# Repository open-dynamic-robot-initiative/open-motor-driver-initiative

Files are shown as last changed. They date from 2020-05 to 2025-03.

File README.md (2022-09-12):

# open-motor-driver-initiative
Open-source driver for brushless motors, following the open dynamic robot initiative 

This contains hardware and firmware for several open source motor control boards all based around TMS320F2838x MCU from Texas Instrument. The boards are designed to perform sensored FOC control of PMSM and BMDC motors.
The goal of this is to provide an alternative to close-sourced industrial grade motor controller that doesn't allow custom control design low, custom communication buses and sensor integration, as well as an alternative to open source low-cost projects that make many compromises and limit their performance.

This should only be replicated for specific needs, where bandwidth, power computation or sensor integration are needed. Often off-shelf solutions offer easier and lower cost solution. 

The TMS320F2838x offer a high number of peripheral dedicated to motor control as well as a fair bit of computational power with 3 CPUs and hardware accelerators. It also offers a range of high bandwidth communication buses such as SPI, FSI, EtherCAT, USART, CAN-FD, Ethernet, USB V2, etc. that allow to implement custom network ideal for centralised robotic applications. 

The main motivation for those boards is for them to be integrated into legged robotics to do academic research. 

All the content of this repository is under BSD-3 Licence.

## Several motor control boards
Several boards are developed around the same system architecture to accommodate different needs. (Number of axis, power ranges, from factor etc.)
See below an overview of the boards

[Todo put picture of all the boards, basic specs and link to the relevant folder]

### Texas Instrument development boards
This setup used TI dev board and was used for first development, It's not a very practical design
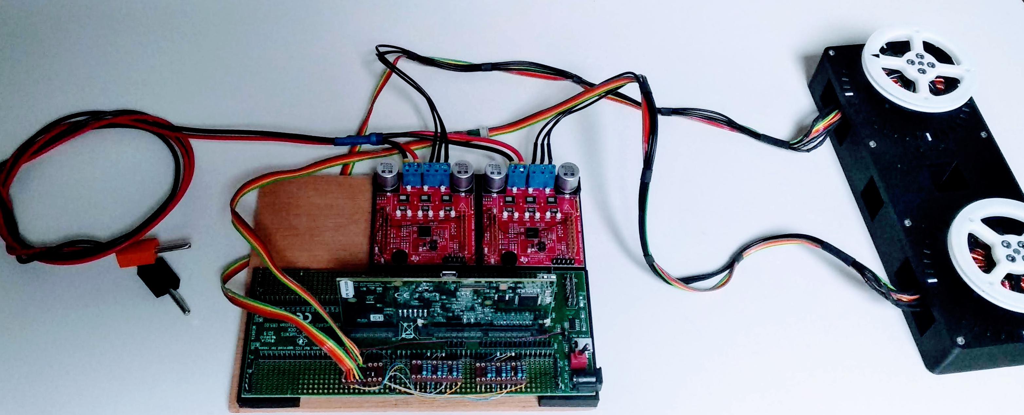
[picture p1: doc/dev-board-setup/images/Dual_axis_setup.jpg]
TI dev boars

### uOmodri (or udriverv3)
This board was design with to be backward compatible with the udriverv2 used in odri robots.
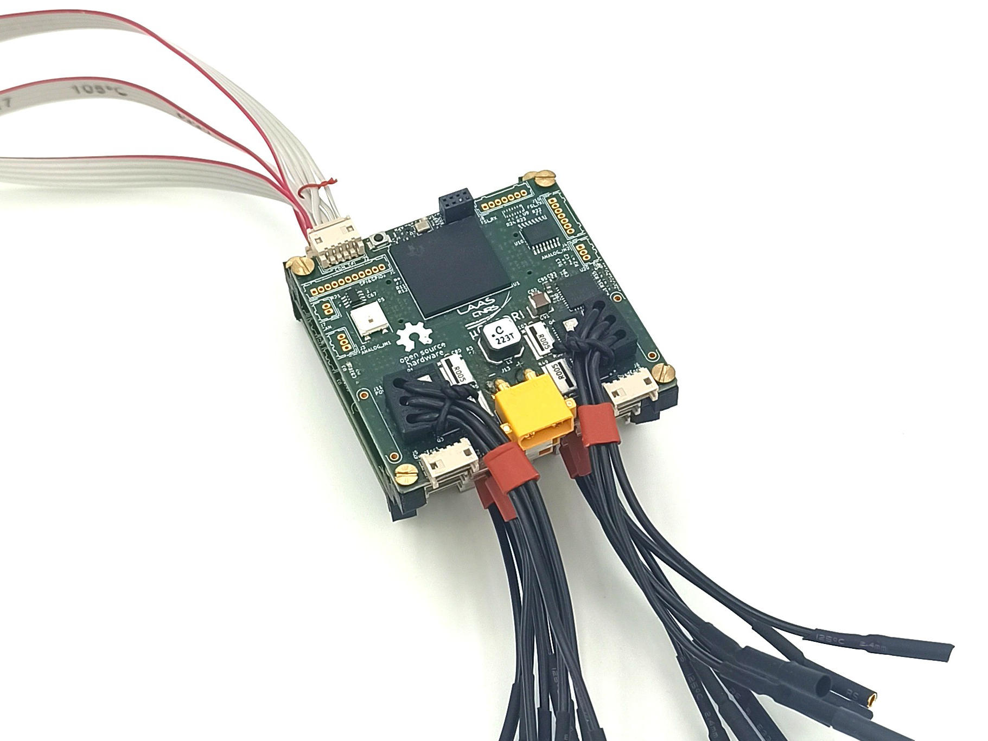
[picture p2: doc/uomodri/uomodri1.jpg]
uomodri

### uOmodri single axis
This board is a project not designed yet. It will be a single-axis version to be attached directly to motors from myactuator.com
### PAL Robotics MC21R01 
[to do]

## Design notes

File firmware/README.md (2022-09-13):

# Software for the Open Motor Driver Initiative project - uOmodri board

## Required installs
In order to use the UOMODRI projects, you must install [Code Composer Studio (CCS)](https://software-dl.ti.com/ccs/esd/documents/ccs_downloads.html) and [C2000Ware library](https://www.ti.com/tool/C2000WARE#downloads) from Texas Instruments. C2000Ware Motor Control SDK is not necessary anymore. 
The [installation](https://software-dl.ti.com/ccs/esd/documents/users_guide/index_installation.html) procedure is available on TI website.
For Linux users, don't forget to install USB drivers (everything is explained on Texas Instrument website).
When installing CCS, prefer a custom installation and check "C2000 real-time MCUs" installation.

## Repository description
This repository contains one project:
	**uOmodri_c28** : Main project. Implements current, speed and position control for PMSM along with a SPI communication for commands or debug. 
3 Files are mainly used for configuration:
- inc\uomodri_user_defines.h : Saves all the defines used in the project.
- inc\uomodri_hal_config_handlers.h : Structures necessaries during initialization phase.
- inc\uomodri_prj_config_handlers.h : Structures used in the running phase of the project.

## How to import these project
After cloning the repository, you can import the projects by doing Project > Import CCS project.
The last thing you must do before being able to compile the projects is to define the path to your C2000Ware library.
To do so, right click on the  project, and then Properties > Resource > Linked Resources.
Now modify the C2000WARE_ROOT path to match your own C2000Ware library folder path.
The folder should be named something like "C2000Ware_4_01_00_00" for the 4.01.00.00 version.
Verify that PARENT_LOC and WORKSPACE_LOC point on your own working workspace.

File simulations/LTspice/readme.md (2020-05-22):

LTspice XVII simulations.

To run the simulations you need to extract the files in the "Support Pack Rev 1.1.zip" and execute the files from inside the folder.

Support Pack Rev 1.1
Source: https://e2e.ti.com/support/archive/motor/m/spice/665327

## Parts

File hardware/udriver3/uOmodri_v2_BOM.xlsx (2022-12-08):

Reference | Value | Qty/PCB | Part No | Footprint | Mouser | DigiKey | Farnell | RS | STOCK
C4, C5, C6, C9, C10, C11, C30, C32, C33, C34, C35, C36, C43, C45, C46, C47, C48, C49 | 1.8nF | 18 | GRM033R71E182KA12D | Capacitor_SMD:C_0201_0603Metric | 81-GRM033R71E182KA2D | 490-GRM033R71E182KA12DTR-ND | 2999522 |  | 300
C29, C42 | 47nF | 2 | C1608X7S2A473K080AB | Capacitor_SMD:C_0603_1608Metric | 810-C1608X7S2A473K | 445-6032-1-ND | 2906791 |  | 100
C3, C7, C8, C12, C13, C14, C19, C20, C21, C22, C23, C26, C31, C39, C44, C50, C51, C52, C53, C54, C55, C69, C72, C73, C74, C75, C76, C77, C78, C79, C80, C81, C82, C83, C84, C85, C86, C87, C88, C89, C90, C91, C92, C93, C94, C99, C100, C101, C102, C103, C104 | 100nF | 51 | GRM033R61E104KE14J | Capacitor_SMD:C_0201_0603Metric | 81-GRM033R61E104KE4J | 490-14571-1-ND | 3790414 | 185-2066 | 1000
C58, C97 | 100nF | 2 | GRM188R72A104KA35D | Capacitor_SMD:C_0603_1608Metric | 81-GRM188R72A104KA35 | 490-3285-1-ND | 1828921 |  | 100+
C1, C2 | 220nF | 2 | GRM033R61C224KE14J | Capacitor_SMD:C_0201_0603Metric | 81-GRM033R61C224KE4J | 490-GRM033R61C224KE14JTR-ND | 3785715 |  | 100
C24, C27, C37, C40 | 1uF | 4 | C1005X5R1V105K050BE | Capacitor_SMD:C_0402_1005Metric | 810-C1005X5R1V105KE | 445-175218-1-ND | 3416060 |  | 150+
C28, C41, C61, C64, C67, C68, C71 | 1uF | 7 | GRM033C81A105ME05D | Capacitor_SMD:C_0201_0603Metric | 81-GRM033C81A105ME5D | 490-13219-1-ND | 3238032 |  | 250+
C25, C38 | 10uF | 2 | GRM188R61E106MA73D | Capacitor_SMD:C_0603_1608Metric | 81-GRM188R61E106MA3D | 490-7202-2-ND | 2695906 | 815-1377 | 100
C56, C57, C95, C96 | 10uF | 4 | C3225X7R1N106K250AC | Capacitor_SMD:C_1210_3225Metric | 810-C3225X7R1N106K25 | 445-C3225X7R1N106K250ACCT-ND | 3416259 |  | 100+
C60, C62, C63, C65, C66, C70 | 10uF | 6 | GRM155R60J106ME15D | Capacitor_SMD:C_0402_1005Metric | 81-GRM155R60J106ME5D | 490-13238-2-ND | 3582794 |  | 100
C15, C16, C17, C18 | 22uF | 4 | C5750X7S2A226M280KB | Capacitor_SMD:C_2220_5650Metric | 810-C5750X7S2A226280 | 445-C5750X7S2A226M280KBCT-ND | 3416277 |  | 60
C59, C98 | 22uF | 2 | GRM21BR61E226ME44L | Capacitor_SMD:C_0805_2012Metric | 81-GRM21BR61E226ME4L | 490-10749-2-ND | 1907510 | 247-8112 | 50
R31, R32, R39, R40, R41, R47 | 0.005 | 6 | FC4L32R005FER | udriver3:FC4L32 | 588-FC4L32R005FER | FC4L32R005FER-ND | 2420555 | 126-0360 | 100
R62, R64, R67, R68 | 10 | 4 | ERJ-1GNF10R0C | Resistor_SMD:R_0201_0603Metric | 667-ERJ-1GNF10R0C | P122669TR-ND | 2302282 | 179-7137 | 100
R18, R19, R20 | 100 | 3 | ERJ-1GNF1000C | Resistor_SMD:R_0201_0603Metric | 667-ERJ-1GNF1000C | P122654CT-ND | 2302309 | 179-7123 | 100+
R5, R6, R27, R30, R33, R34, R35, R42, R43, R44, R55, R56 | 120 | 12 | ERJ-1GNF1200C | Resistor_SMD:R_0201_0603Metric | 667-ERJ-1GNF1200C | P122692CT-ND | 2396857 |  | 200+
R58 | 909 | 1 | ERJ-1GNF9090C | Resistor_SMD:R_0201_0603Metric | 667-ERJ-1GNF9090C | P123194TR-ND | 3303125 |  | 100
R7, R8, R9, R10, R11, R12, R17, R37, R45 | 1k | 9 | ERJ-1GNF1001C | Resistor_SMD:R_0201_0603Metric | 667-ERJ-1GNF1001C | P122413CT-ND | 2302336 | 179-7127 | 200+
R50 | 2.49k | 1 | ERJ-1GNF2491C | Resistor_SMD:R_0201_0603Metric | 667-ERJ-1GNF2491C | P122865TR-ND | 3335222 |  | 100
R25 | 5.1k | 1 | ERJ-2RKF5101X | Resistor_SMD:R_0402_1005Metric | 667-ERJ-2RKF5101X | P5.10KLCT-ND | 2302709 | 732-5536 | 200+
R1, R2, R3, R4, R14, R15, R16, R21, R22, R23, R26, R28, R29, R36, R38, R46, R48, R57, R59, R60, R61, R65, R66 | 10k | 23 | ERJ-1GNF1002C | Resistor_SMD:R_0201_0603Metric | 667-ERJ-1GNF1002C | P122414CT-ND | 2302362 | 176-3597 | 400+
R52 | 22.1k | 1 | ERJ-1GNF2212C | Resistor_SMD:R_0201_0603Metric | 667-ERJ-1GNF2212C | P122837CT-ND | 3335196 |  | 100+
R13, R49, R51, R53, R54 | 100k | 5 | ERJ-1GNF1003C | Resistor_SMD:R_0201_0603Metric | 667-ERJ-1GNF1003C | P122655CT-ND | 2302389 | 179-7130 | 200+
R24 | 100k | 1 | ERJ-2RKF1003X | Resistor_SMD:R_0402_1005Metric | 667-ERJ-2RKF1003X | P100KLCT-ND | 2302839 | 732-5255 | 200+
FB1, FB2, FB3 | 220R@100MHz | 3 | BLM18SG221TN1D | Inductor_SMD:L_0603_1608Metric | 81-BLM18SG221TN1D | 490-5225-1-ND | 1515753 | 792-6271 | 100
U1, U2, U3, U19 | 74LVC2G17 | 4 | 74LVC2G17GM,115 | udriver3:SOT886_USON_6_1.45x1.0mm_P0.5mm | 771-LVC2G17GM115 | 1727-7017-2-ND |  |  | 50
J8, J9 | ADM6_ADF6 | 2 | ADF6-10-03.5-L-4-2-A | udriver3:ADF6-10-XX.X-XXX-4-X-A-XR | 200-ADF6-10-3.5-L42A | 612-ADF6-10-03.5-L-4-2-A-TR-ND | 3462763 | 202-7885
SW1 | B3U-3100P-B | 1 | B3U-1000P-B | Button_Switch_SMD:SW_SPST_B3U-1000P-B | 653-B3U-1000P-B | SW1143TR-ND | 1333654 |  | 50
D2 | BAT54L | 1 | BAT54L,315 | Diode_SMD:D_0402_1005Metric | 771-BAT54L-T/R | 2156-BAT54L,315-954-ND | 2438976 |  | 25
U16 | BMI088 | 1 | BMI088 | udriver3:Bosch_LGA-16_4.5x3.0mm_P0.5mm | 262-BMI088 | 828-1082-2-ND |  |  | 5+10
J6 | Conn_01x02 | 1 |  | udriver3:AMASS_XT30PW-M_1x02_P2.50mm_Horizontal
J13 | conn_01x02_MountingPins | 1 | DF13-2P-1.25H(76) | udriver3:Hirose_DF13_02P-1.25H_1x02_P1.25mm_Right_angle | 798-DF13-2P-1.25H76 | H126390-ND |  | 188-5752 | 30
J10, J11 | Conn_01x03 | 2 |  | udriver3:AMASS_MR30PW-FB_1x03_P3.50mm_Horizontal
J1 | conn_01x04_MountingPins | 1 | DF13-4P-1.25H(76) | udriver3:Hirose_DF13_04P-1.25H_1x05_P1.25mm_Right_angle | 798-DF13-4P-1.25H76 | H126400-ND | 2916344 | 188-6267 | 30
J2, J3, J14 | conn_01x05_MountingPins | 3 | DF13-5P-1.25H(76) | udriver3:Hirose_DF13_05P-1.25H_1x05_P1.25mm_Right_angle | 798-DF13-5P-1.25H76 | H126405-ND | 3019728 | 188-6306 | 100
J4, J5 | conn_01x08_MountingPins | 2 | 5034800800 | udriver3:Molex_FBH1_1x08-2MP_P0.50mm_Horizontal | 538-503480-0800 | WM1388TR-ND | 2396218 | 896-7614 | 50
J12 | Conn_01x10 | 1 | DF13-10P-1.25DSA | udriver3:Hirose_DF13-10P-1.25DSA_1x10_P1.25mm_Vertical | 798-DF13-10P-1.25DSA | H2198-ND |  | 188-6354 | 11+10
J7 | Conn_02x04_Odd_Even | 1 | 20021311-00008T4LF | udriver3:PinSocket_2x04_P1.27mm_Vertical | 649-221311-00008T4LF | 609-3753-ND | 2892503 |  | 40
Q2, Q3, Q4, Q5, Q6, Q7 | CSD88599Q5DC | 6 | CSD88599Q5DC | udriver3:VSON_CLIP_22 | 595-CSD88599Q5DC | 296-48289-1-ND | 2766880 |  | 130 + 50 (CSD88584)
U9, U10 | DRV8353S | 2 | DRV8353SRTAT | Package_DFN_QFN:QFN-40-1EP_6x6mm_P0.5mm_EP4.6x4.6mm_ThermalVias | 595-DRV8353SRTAT | 296-DRV8353SRTATCT-ND |  |  | 11+50(SMRTAT)
U4 | DSLVDS1047 | 1 | DSLVDS1047PWR | Package_SO:TSSOP-16_4.4x5mm_P0.65mm | 595-DSLVDS1047PWR | 296-50740-1-ND |  |  | 50
U5 | DSLVDS1048 | 1 | DSLVDS1048PWR | Package_SO:TSSOP-16_4.4x5mm_P0.65mm | 595-DSLVDS1048PWR | 296-51106-1-ND |  |  | 35
X1 | ECS-TXO-2016 | 1 | ECS-TXO-2016-33-250-TR | udriver3:TCXO_SMD_Ecs_TXO-2016-4Pin_2.0x1.6mm | 520-TXO-2016-33-250T | XC3163TR-ND | 4059413 |  | 50
D11, D12 | ESD321 | 2 | ESD321DPYR | Diode_SMD:D_0402_1005Metric | 595-ESD321DPYR | 296-51108-1-ND |  |  | 100+
D6 | LED GREEN | 1 | HSMG-C280 | LED_SMD:LED_0402_1005Metric | 630-HSMG-C280 | 516-3066-1-ND | 2494322 | 867-6560 | 200
D9, D10 | LED RED | 2 | HSMC-C280 | LED_SMD:LED_0402_1005Metric | 630-HSMC-C280 | 516-3060-1-ND | 2494321 |  | 100
U14 | LT6654AIS6-3 | 1 | LT6654AIS6-3#TRMPBF | Package_TO_SOT_SMD:TSOT-23-6 | 584-6654AIS63TRMPBF | LT6654AIS6-3#TRMPBFCT-ND | 2761957 |  | 35
U12, U13 | MPM3804GG | 2 | MPM3804GG | udriver3:QFN-10_2x2mm_P0.5mm | 946-MPM3804GG-Z | 1589-1982-1-ND | 3358188 |  | 100
Q1 | NX7002BKM | 1 | NX7002BKMYL | Package_DFN_QFN:Diodes_DFN1006-3 | 771-NX7002BKMYL | 1727-2232-1-ND | 2498574 |  | 50
U17 | TCAN330G | 1 | TCAN330GDCNR | Package_TO_SOT_SMD:TSOT-23-8 | 595-TCAN330GDCNR | 296-TCAN330GDCNRTR-ND | 3009407 |  | 50
U18 | THVD24x0 | 1 | THVD2450DRBR | udriver3:VSON-8-1EP_3.0x3.0mm_P0.65mm_EP1.65x2.4mm | 595-THVD2450DRBR | 296-THVD2450DRBRTR-ND |  |  | 50
U6 | TMS320F28388D | 1 | F28388DZWTS | udriver3:NFBGA_337 | 595-F28388DZWTS | 296-F28388DZWTS-ND |  |  | 20 + 18(F28386)
D5, D7, D8 | TPD1E04U04 | 3 | TPD1E04U04DPLT | Diode_SMD:D_0402_1005Metric | 595-TPD1E04U04DPLT | 296-47862-1-ND |  |  | 50
D1, D3 | TPD6E05U06 | 2 | TPD6E05U06RVZR | udriver3:USON_14 | 595-TPD6E05U06RVZR | 296-39349-1-ND |  |  | 200
U8 | TPS3703-1.2 | 1 | TPS3703A7120DSERQ1 | Package_SON:WSON-6_1.5x1.5mm_P0.5mm | 595-S3703A7120DSERQ1 | 296-TPS3703A7120DSERQ1CT-ND |  |  | 50
U7 | TPS3703-3.3 | 1 | TPS3703A7330DSERQ1 | Package_SON:WSON-6_1.5x1.5mm_P0.5mm | 595-S3703A7330DSERQ1 | 296-TPS3703A7330DSERQ1CT-ND |  |  | 50
U15 | TPSM560R6H | 1 | TPSM560R6HRDAR | udriver3:B3QFN_15 | 595-TPSM560R6HRDAR | 296-TPSM560R6HRDARTR-ND |  |  | 50
U11 | TPSM5601R5 | 1 | TPSM5601R5RDAR | udriver3:B3QFN_15 | 595-TPSM5601R5SRDAR | 296-TPSM5601R5RDARTR-ND |  |  | 50
J15 | USB_B_Micro | 1 | 473460001 | udriver3:USB_Micro-B_Molex_47346-0001 | 538-47346-0001 | WM17141CT-ND | 1568026 | 702-5475 | 30
D4 | WS2812B | 1 | WS2812B 5050 | LED_SMD:LED_WS2812B_PLCC4_5.0x5.0mm_P3.2mm | 474-COM-16346 | 1568-COM-16347CT-ND |  |  | 50

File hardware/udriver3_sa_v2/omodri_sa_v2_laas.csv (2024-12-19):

Id | Designator | Footprint | Quantity | Designation | Supplier and ref
1 | C51,C45 | C_0402_1005Metric | 2 | 1u
2 | C50,C48,C66,C63,C65,C70,C102,C101,C62,C64,C2,C61,C67,C27,C6,C5,C9,C4,C25,C29,C28,C69,C21,C31,C30,C68,C22,C19,C20,C24,C23,C26,C13,C16,C38,C7,C14,C42,C87,C18,C3,C37,C41,C8,C15,C17 | C_0201_0603Metric | 46 | 100n
3 | C76,C71,C75,C74,C72,C73 | C_1206_3216Metric | 6 | 4.7u
4 | C53 | C_0603_1608Metric | 1 | 47n
5 | C52,C100,C10,C11,C32,C34,C33,C43,C35,C39 | C_0201_0603Metric | 10 | 1u
6 | C55,C47,C104,C97,C60,C58,C57,C59 | C_0201_0603Metric | 8 | 1.8n
7 | FB3,FB1,FB2 | R_0603_1608Metric | 3 | 220
8 | R1,R52,R30,R54,R8,R9,R10,R25,R35,R33,R34,R32,R11,R29,R12,R36,R26,R31,R6 | R_0201_0603Metric | 19 | 10k
9 | U13,U14 | QFN-10_2x2mm_P0.5mm | 2 | MPM3804GG-Z
10 | R27,R16,R19 | FC4L32 | 3 | 0.005
11 | U5 | UQFN-10_1.5x2mm_P0.5mm | 1 | TS3USB221E
12 | Q1,Q2,Q3 | VSON_CLIP_22 | 3 | CSD88599Q5DC
13 | R43,R44,R49,R46,R48,R40,R41 | R_0201_0603Metric | 7 | 100k
14 | R15,R18,R21 | R_0805_2012Metric | 3 | 4.7
15 | R50 | R_0201_0603Metric | 1 | 6.84k
16 | U7 | Bosch_LGA-16_4.5x3.0mm_P0.5mm | 1 | BMI088
17 | R37,R51,R24,R13,R14,R23,R22,R4 | R_0201_0603Metric | 8 | 120
18 | R53 | R_0201_0603Metric | 1 | 6.22k
19 | U4 | SOT-23-8 | 1 | TCAN3414
20 | R45 | R_0201_0603Metric | 1 | 13.7k
21 | Q4 | Diodes_DFN1006-3 | 1 | NX7002BKM
22 | C49,C91,C90,C92,C89 | C_0603_1608Metric | 5 | 10u
23 | D6 | LED_0402_1005Metric | 1 | LED GREEN
24 | U12 | uSIP_11 | 1 | TPSM8290x
25 | J3 | SAMTEC_CLP-104-02-L-D-BE | 1 | SAMTEC_CLP_02x04_SMD
26 | R2,R3,R5,R7 | R_0201_0603Metric | 4 | 10
27 | X1 | TCXO_SMD_Ecs_TXO-2016-4Pin_2.0x1.6mm | 1 | ECS-TXO-2016
28 | C93,C99,C96,C94,C44,C98,C95,C40,C36,C12 | C_0402_1005Metric | 10 | 10u
29 | U1 | NFBGA_337 | 1 | TMS320F28388D
30 | U15 | TSOT-23-6 | 1 | LT6654AIS6-3
31 | D5,D4 | NeoPixel_SK6805_1.5x1.5mm | 2 | NeoPixel_1515
32 | D2,D7,D1 | D_0201_0603Metric | 3 | TPD1E04U04
33 | U2 | QFN-40-1EP_6x6mm_P0.5mm_EP4.6x4.6mm | 1 | DRV8353S
34 | C88 | C_0603_1608Metric | 1 | 100n
35 | SW1 | SW_SPST_B3U-1000P-B | 1 | B3U-1000P-B
36 | R47 | R_0201_0603Metric | 1 | 22.1k
37 | TP1 | TestPoint_Keystone_5015_Micro-Minature | 1 | GND
38 | U16 | SOT-353_SC-70-5 | 1 | OPA333xxDCK
39 | C103,C1 | C_0201_0603Metric | 2 | 220n
40 | C82,C83,C77,C86,C84,C85,C81,C79,C80,C78 | C_1210_3225Metric | 10 | 10u
41 | C54,C46,C56 | C_0402_1005Metric | 3 | 4.7n
42 | R20,R28,R17 | R_0805_2012Metric | 3 | 2.2
43 | R38 | R_0402_1005Metric | 1 | 100k
44 | U8 | SOT886_USON_6_1.45x1.0mm_P0.5mm | 1 | 74LVC1G17
45 | R42 | R_0201_0603Metric | 1 | 9.09k
46 | R39 | R_0402_1005Metric | 1 | 5.1k
47 | U9 | WSON-6_1.5x1.5mm_P0.5mm | 1 | TPS3703-3.3
48 | U10 | WSON-6_1.5x1.5mm_P0.5mm | 1 | TPS3703-1.2
49 | J2 | Molex_FBH1_FFC_FPC_503480-2000_1x20-2MP_P0.50mm_Horizontal | 1 | conn_01x20_MountingPins
50 | D3 | TI_X2SON-3_1.3x0.6mm_P1.0mm | 1 | ESD122
51 | U6 | VSON-8-1EP_3.0x3.0mm_P0.65mm_EP1.65x2.4mm | 1 | THVD2450
52 | U11 | B3QFN_15 | 1 | TPSM560R6H
53 | U3 | TSSOP-14_4.4x5mm_P0.65mm | 1 | AS5047U

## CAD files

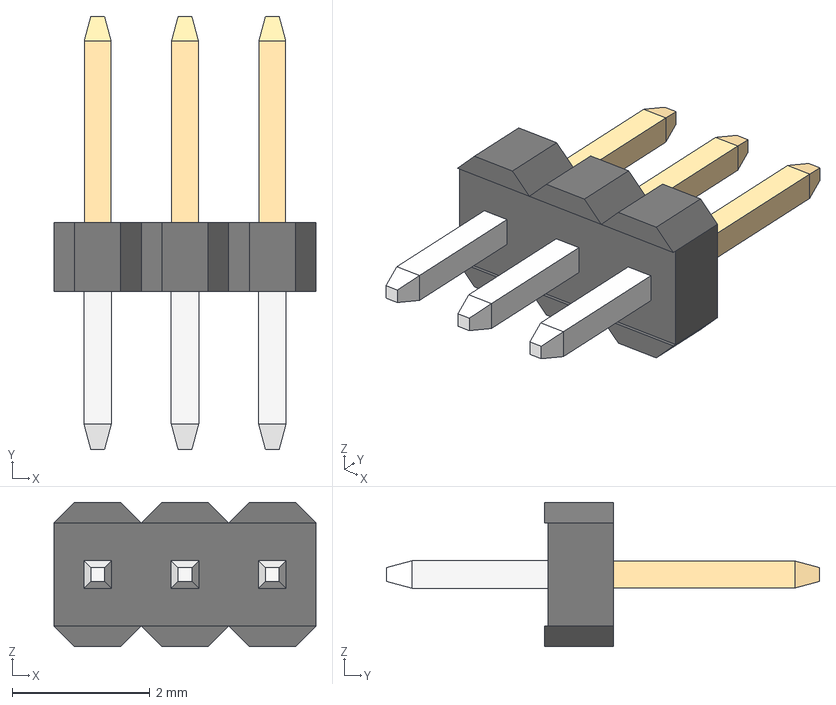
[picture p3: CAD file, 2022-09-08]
hardware/EcatExBrd/3D/Harwin_3P_m50-3530342_asm.stp
3.81 x 6.30 x 2.10 mm
M50-35303_MOULD
M50-353_CONTACT x 3

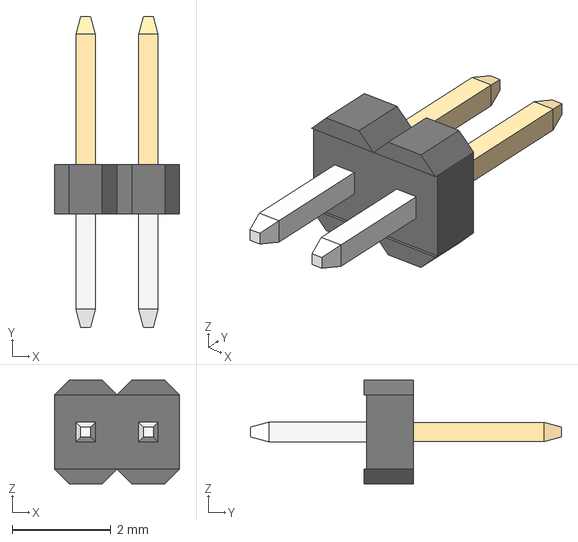
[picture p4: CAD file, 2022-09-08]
hardware/EcatExBrd/3D/Harwin_2P_m50-3530242_asm.stp
2.54 x 6.30 x 2.10 mm
M50-35302_MOULD
M50-353_CONTACT x 2

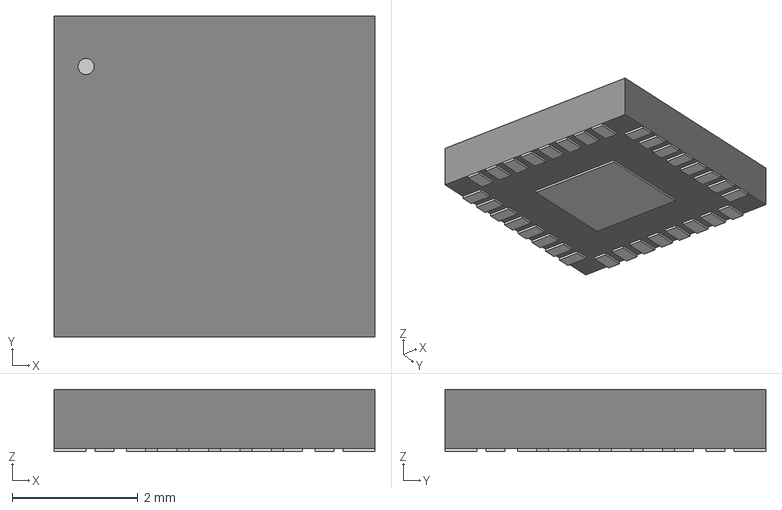
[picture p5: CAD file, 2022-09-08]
hardware/EcatExBrd/3D/QFN_ERHBR_TEX-L.step
5.11 x 5.11 x 0.993 mm

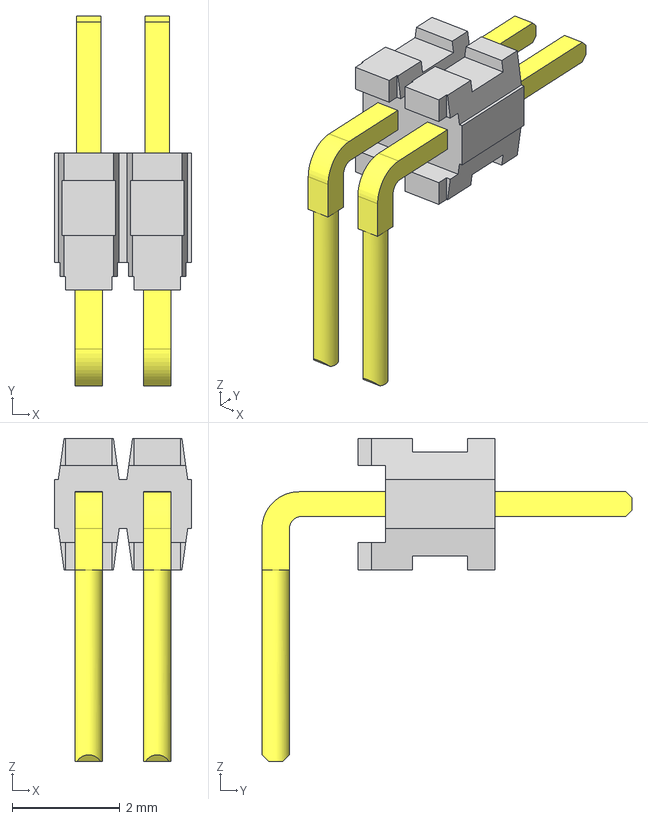
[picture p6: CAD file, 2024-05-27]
hardware/udriver3/3D/SAMTEC_TMS-102-02-G-S-RA.stp
2.54 x 6.86 x 5.99 mm
TMS-102-S_header
T-1M6-02-02-S-RA

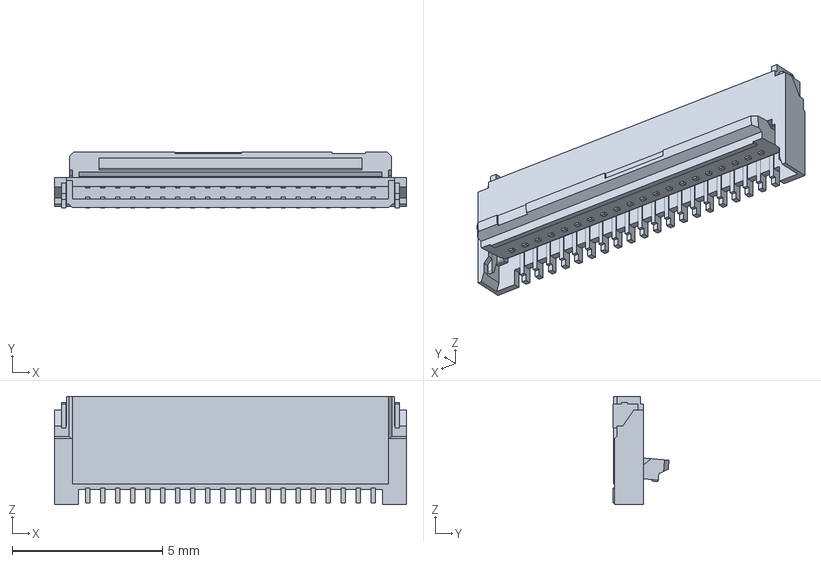
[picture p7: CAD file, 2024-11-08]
hardware/udriver3_sa_v2/3D/MOLEX_5034802000.stp
11.7 x 1.87 x 3.60 mm

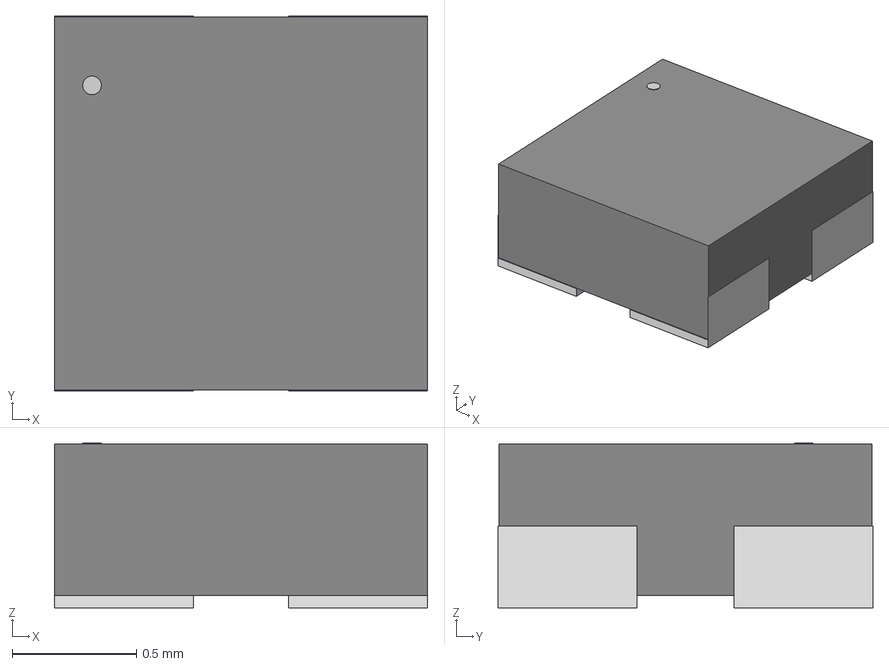
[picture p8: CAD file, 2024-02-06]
hardware/udriver3/3D/NeoPixel_1515_SK6805.step
1.50 x 1.51 x 0.663 mm

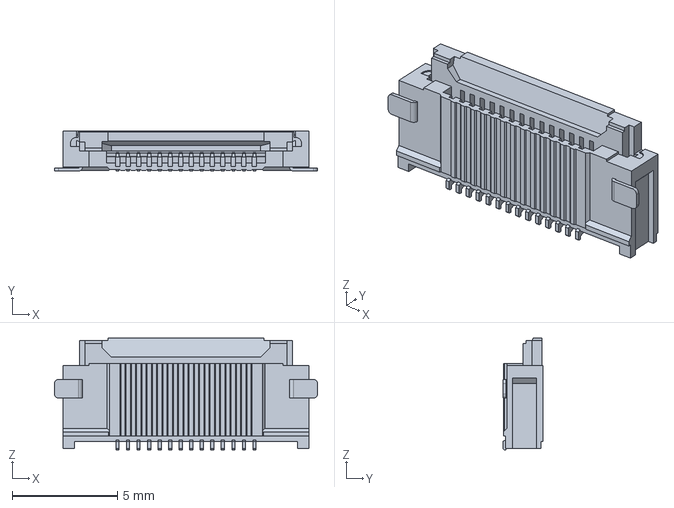
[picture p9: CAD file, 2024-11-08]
hardware/udriver3_sa_v2/3D/MOLEX_5051101497.stp
12.5 x 1.90 x 5.30 mm

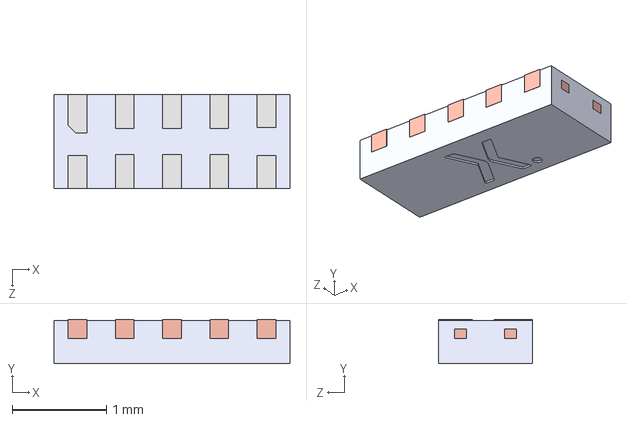
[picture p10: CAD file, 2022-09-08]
hardware/EcatExBrd/3D/Nexperia_IP4283CZ10_DFN2510A-10_SOT1176.step
2.50 x 0.47 x 1.00 mm
SOT1176 LF
SOT1176 Mold body

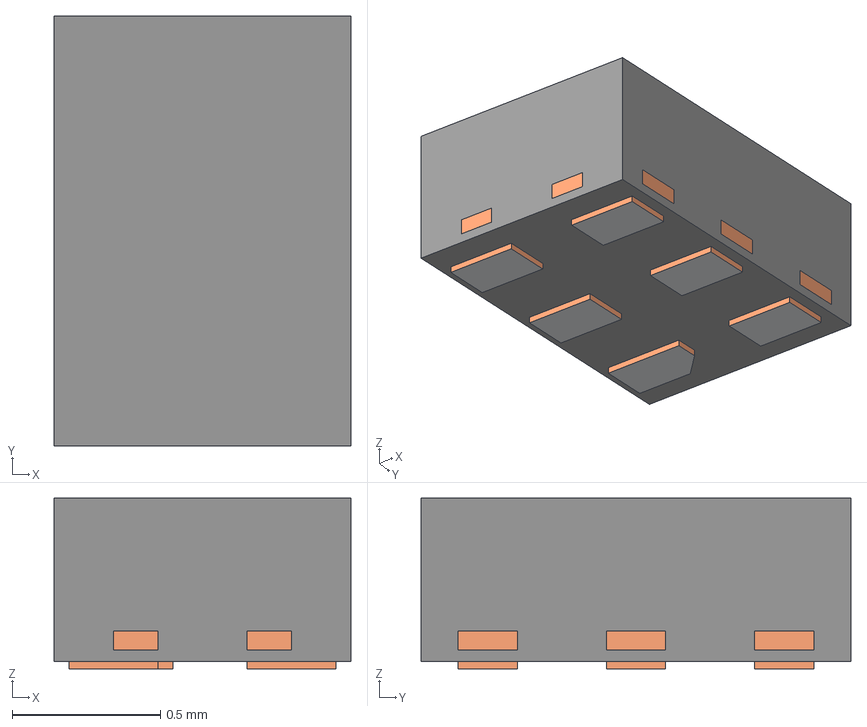
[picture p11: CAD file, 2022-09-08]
hardware/udriver3/3D/DRY0006A.stp
1.00 x 1.45 x 0.575 mm
BODY-SON
FRAME-DRY0006A
PIN1-ID

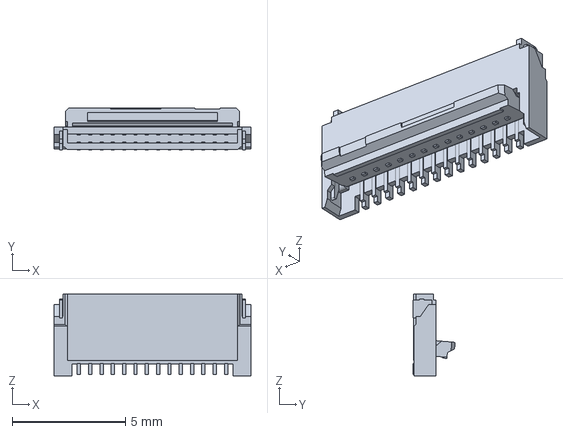
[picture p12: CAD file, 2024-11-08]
hardware/udriver3_sa_v2/3D/MOLEX_5034801400.stp
8.70 x 1.87 x 3.60 mm

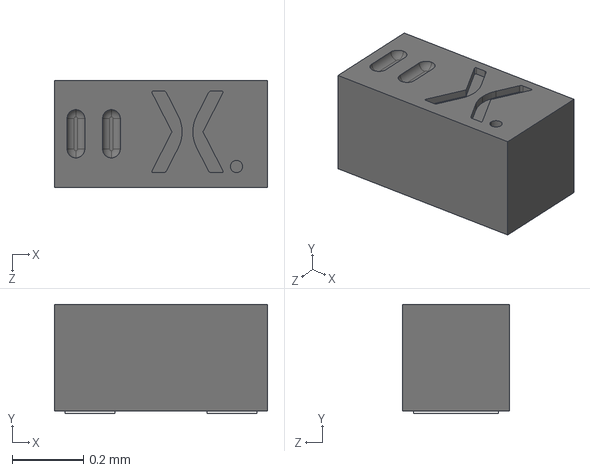
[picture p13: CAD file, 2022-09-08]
hardware/EcatExBrd/3D/Nexperia_PESD6V5C1USF_DSN0603-2_SOD962.step
0.6 x 0.308 x 0.3 mm

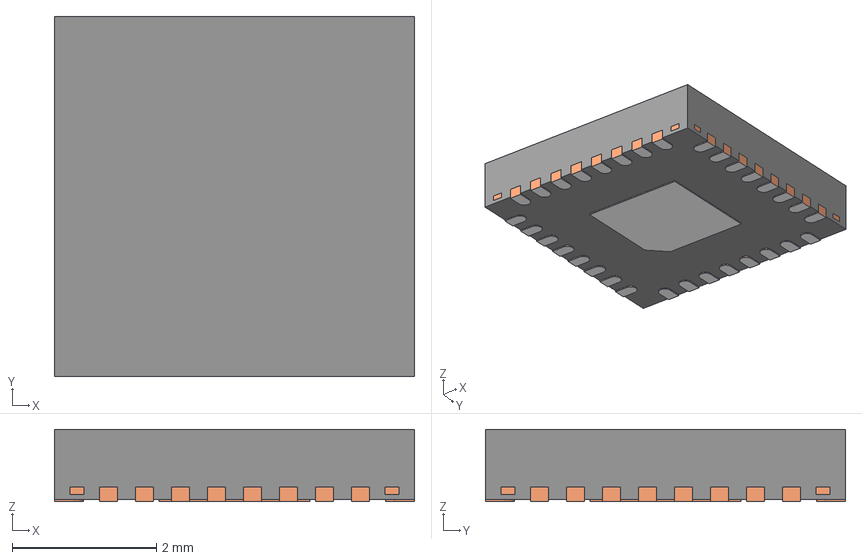
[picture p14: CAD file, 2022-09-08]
hardware/EcatExBrd/3D/RHB0032M.stp
5.00 x 5.00 x 1.00 mm
BODY-QFN
FRAME-RHB0032M
PIN1-ID

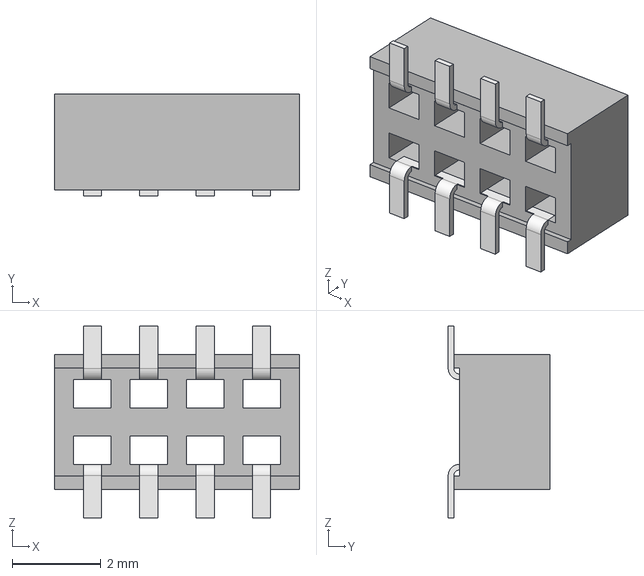
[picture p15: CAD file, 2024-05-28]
hardware/udriver3_sa_v2/3D/SAMTEC_CLP-104-02-L-D-BE.stp
5.51 x 2.29 x 4.32 mm
CLP-104-2-L-D-BE_terminal
C-106-22-1-L-04-BE_Pin x 2

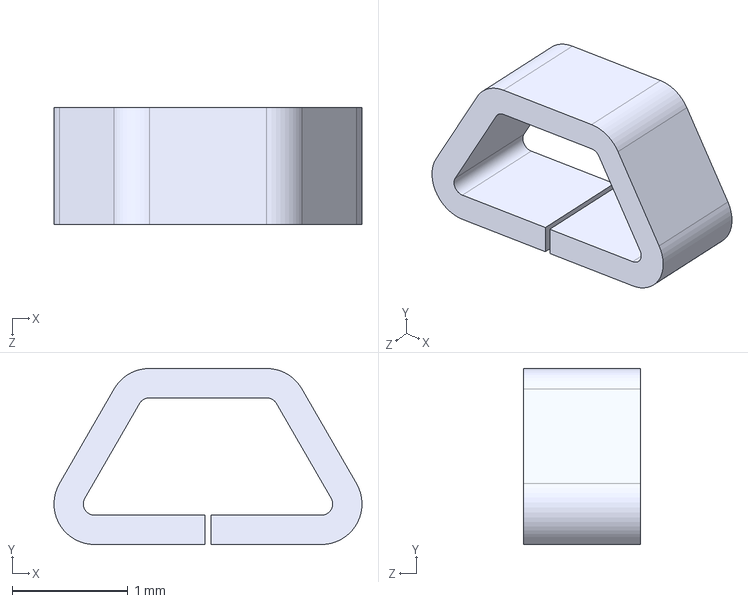
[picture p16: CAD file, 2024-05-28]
hardware/udriver3_sa_v2/3D/KEYSTONE_5015.step
2.67 x 1.52 x 1.02 mm

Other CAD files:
hardware/udriver3_sa_v2/3D/MOLEX_5051101492.stp
hardware/EcatExBrd/3D/QFN_ERHBR_TEX.step
hardware/EcatExBrd/3D/ADM6-10-01.5-L-4-2-A-TR.stp
hardware/udriver3_sa_v2/3D/KEYSTONE_5019.step
hardware/EcatExBrd/3D/DF13-6P-1.25DSA.stp
hardware/EcatExBrd/3D/DF13-8P-1.25DSA.stp
hardware/EcatExBrd/3D/MagJack_RJ45_Molex_480749101.stp
hardware/EcatExBrd/3D/Maxim_max147xx_TDFN8_1EP.step
hardware/EcatExBrd/3D/Maxim_max3107_TQFN24.step
hardware/EcatExBrd/3D/QFN_ERHBR_TEX-M.step
hardware/udriver3_sa_v2/3D/AMASS_MR30PB-FB.step
hardware/udriver3_sa_v2/3D/AMASS_MR30PW-FB.STEP
hardware/udriver3_sa_v2/3D/AMASS_MR30PW-M.STEP
hardware/udriver3_sa_v2/3D/AMASS_XT30PW-M.STEP
hardware/udriver3_sa_v2/3D/AMPHENOL_10165448-00008.stp
hardware/udriver3_sa_v2/3D/ASTX-H12.STEP
hardware/udriver3_sa_v2/3D/BOSCH_BMI088.STEP
hardware/udriver3_sa_v2/3D/C5750X7S2A226M280KB.STEP
hardware/udriver3_sa_v2/3D/Coilcraft-LPS6235.STEP
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

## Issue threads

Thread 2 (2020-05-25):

Labeling error in OMODRI_EtherCAT_x

Jmanhes, 2020-05-25:
In OMODRI_EtherCAT_0 & OMODRI_EtherCAT_1 there is twice the same label : Led0/Strap2.
Must be rename.

Jmanhes, 2020-05-25:
In OMODRI_Support, R193/R194 are connected to U23.
According to CDCLVC1104 datasheet [https://www.ti.com/lit/ds/symlink/cdclvc1104.pdf?ts=1590417975450](url), page 10/32, Table 1 : output logic table.
If 1G=L =>Yn=L whatever CLKin
if 1G=H => Yn=CLKin
So R194/R193 can be removed and pin can by tied to VDD_3V3

Jmanhes, 2020-06-22:
Correction done.

Closed 2020-06-22.

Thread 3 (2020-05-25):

Extra resistors can be removed in OMODRI_Support

Jmanhes, 2020-05-25:
In OMODRI_Support, R193/R194 are connected to U23.
According to CDCLVC1104 datasheet https://www.ti.com/lit/ds/symlink/cdclvc1104.pdf?ts=1590417975450, page 10/32, Table 1 : output logic table.
If 1G=L =>Yn=L whatever CLKin
if 1G=H => Yn=CLKin
So R194/R193 can be removed and pin can by tied to VDD_3V3

nswdc, 2020-07-06:
Closed by comit ba2ab1a811792042321e827a74f1fd63dcaec834

Closed 2020-07-06.

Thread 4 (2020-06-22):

Pin changes

otrebla333, 2020-06-22:
Review pin affectation list to make space for using all available SPI pins and for easing the routing of the EtherCAT lines. Affected pins are:
-Quadrature encoder 2 (move to other space)
- DRV1: nFault
- DRV2: Enable, CS, nFault

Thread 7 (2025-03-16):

Is posible control motor by step/dir??

artayasa, 2025-03-16:
Hi mate
Is posible to control the motor by step/dir?? I want to coustem the power bridge to handle 110v-220v i wamt run pmsm motor by step/dir mate, with abz encoder 20bit or 2000ppr.

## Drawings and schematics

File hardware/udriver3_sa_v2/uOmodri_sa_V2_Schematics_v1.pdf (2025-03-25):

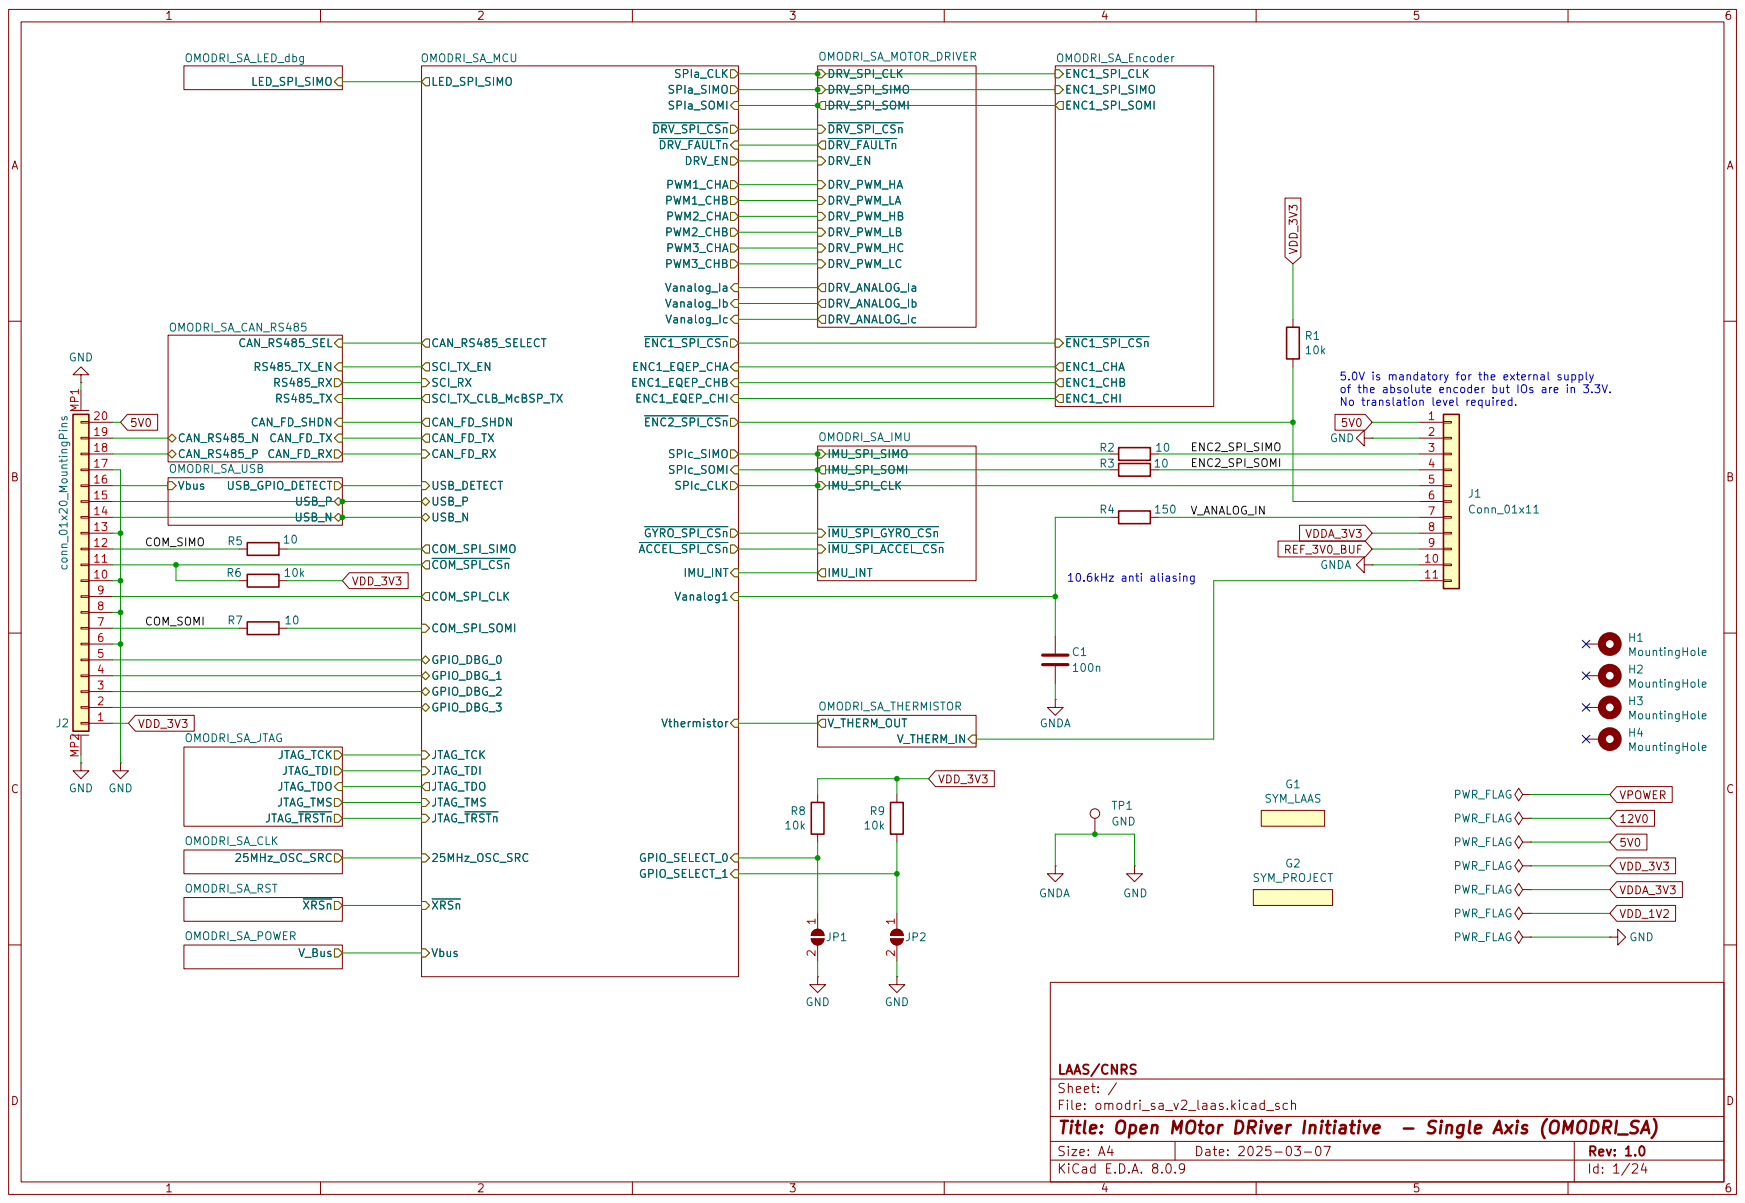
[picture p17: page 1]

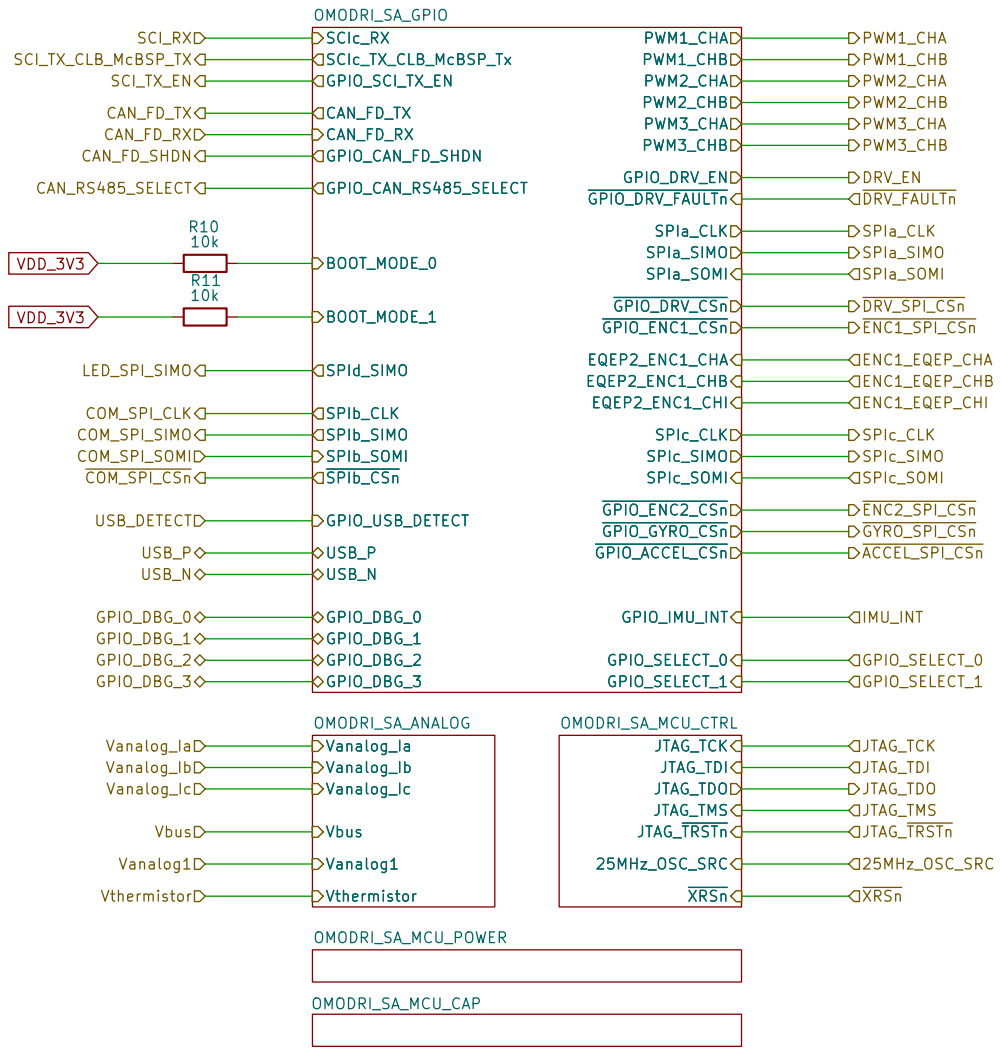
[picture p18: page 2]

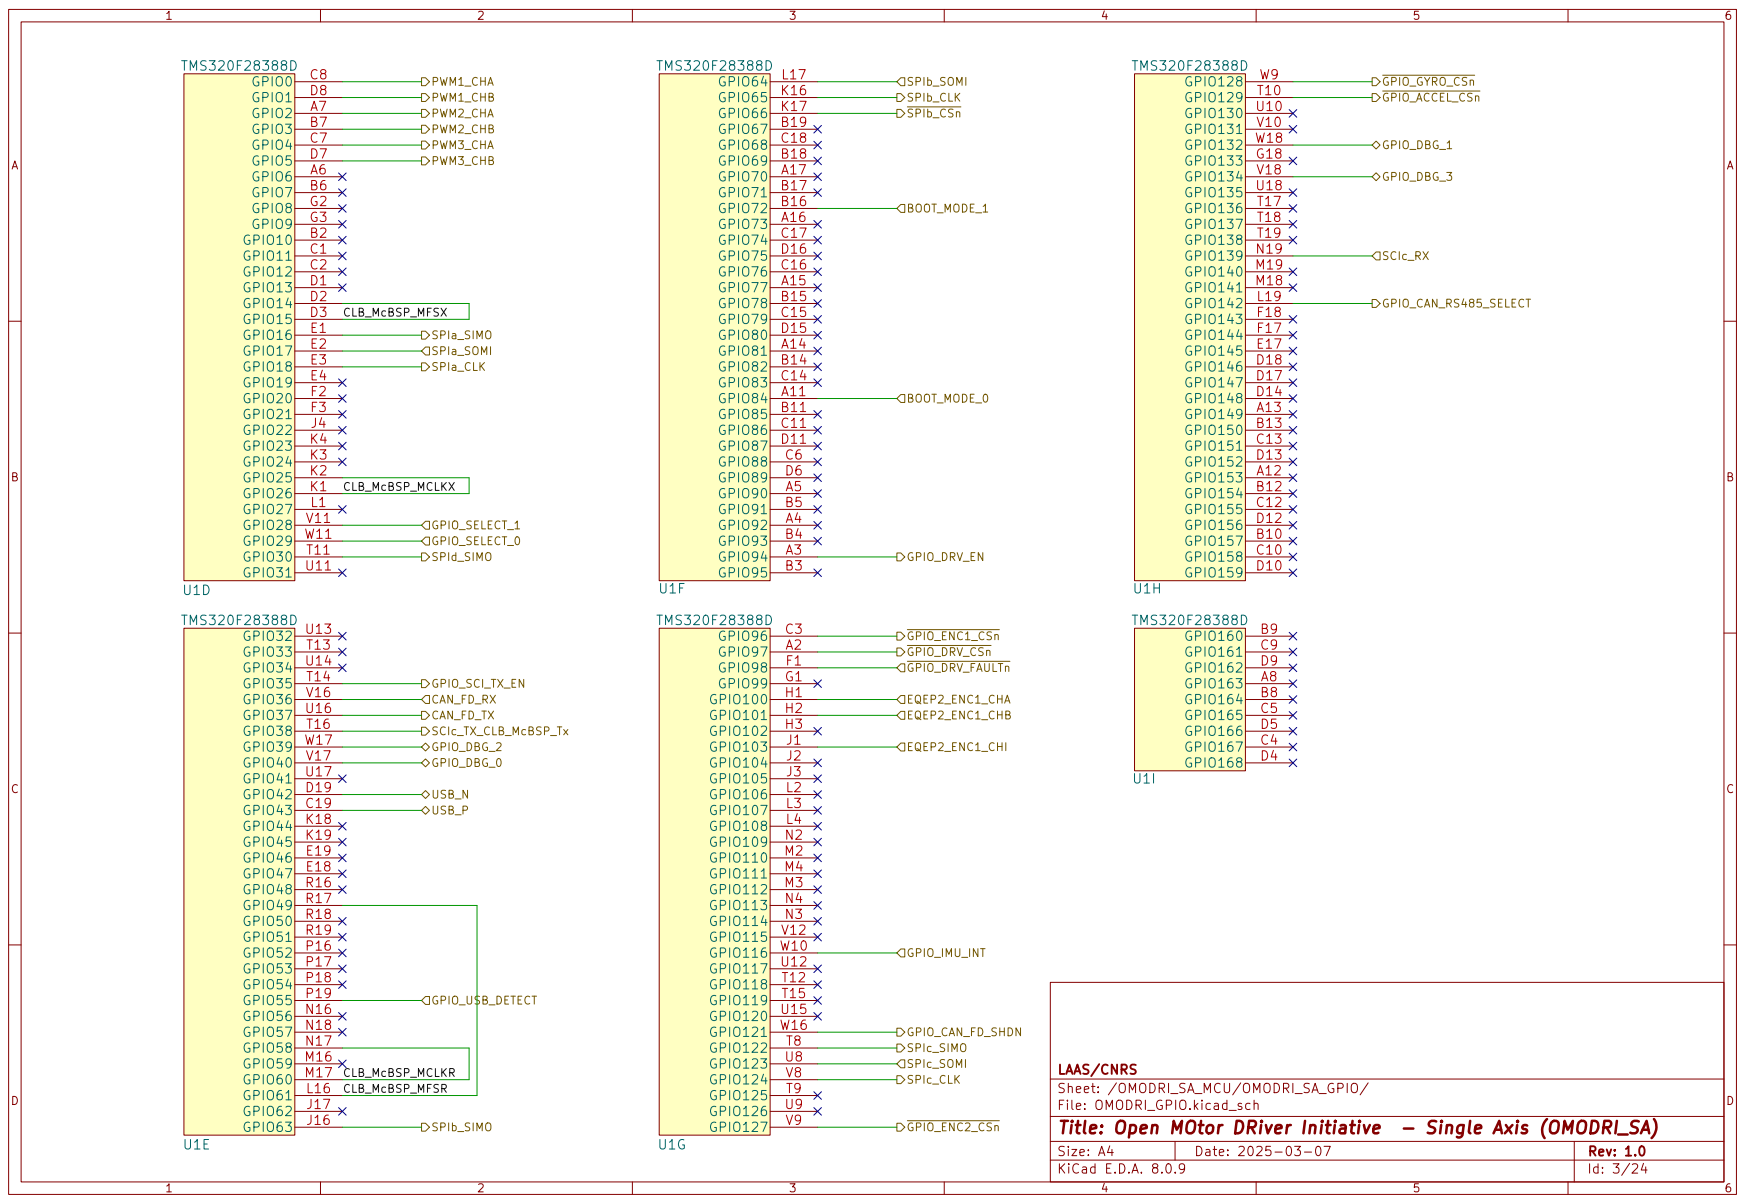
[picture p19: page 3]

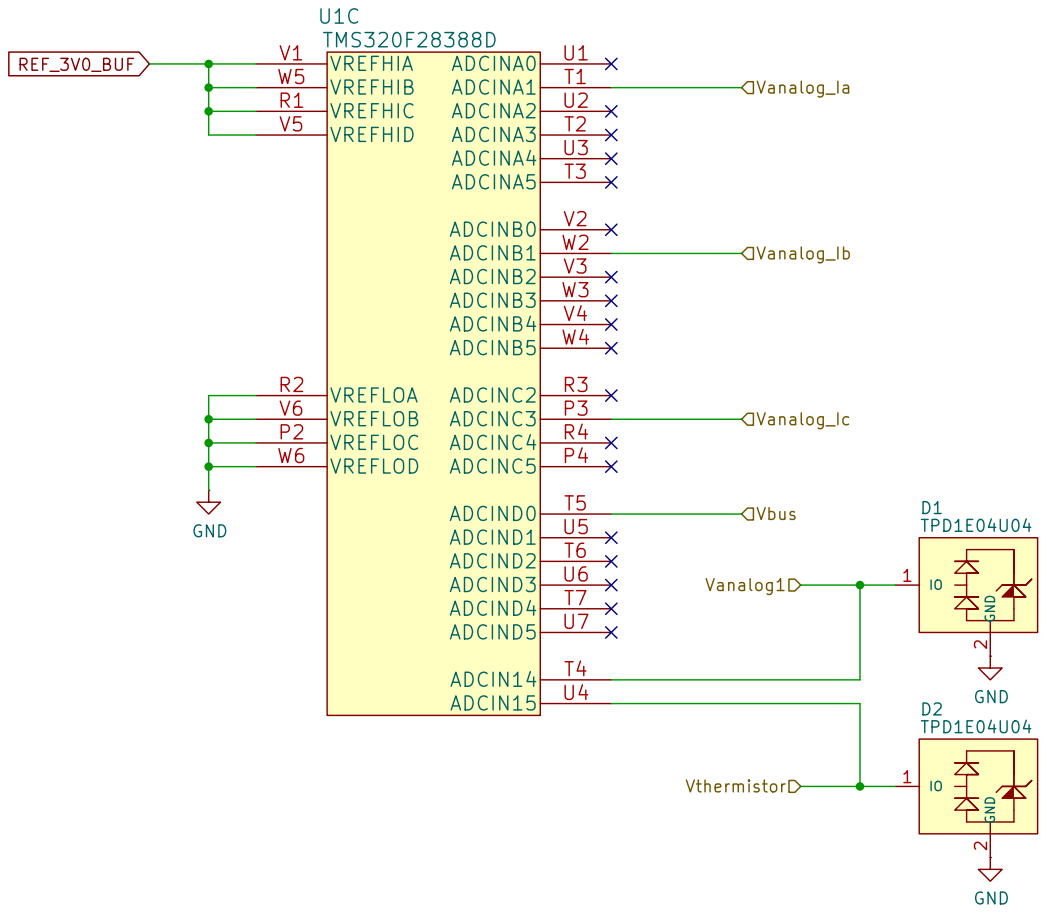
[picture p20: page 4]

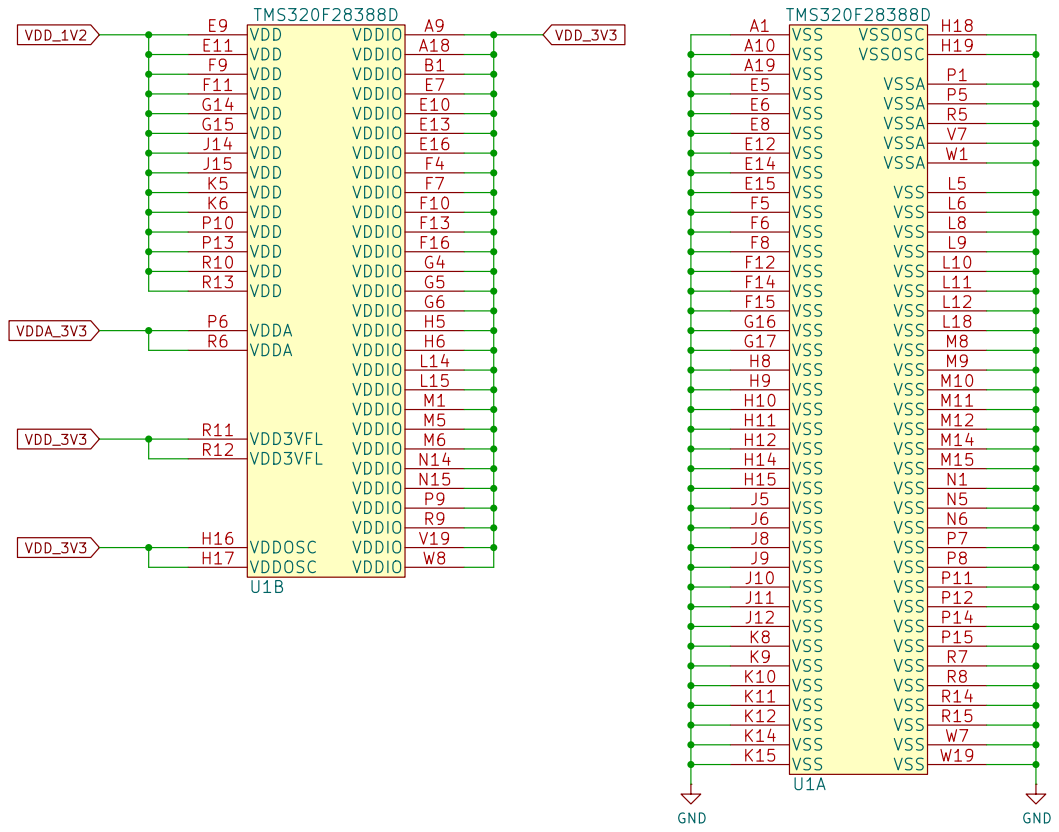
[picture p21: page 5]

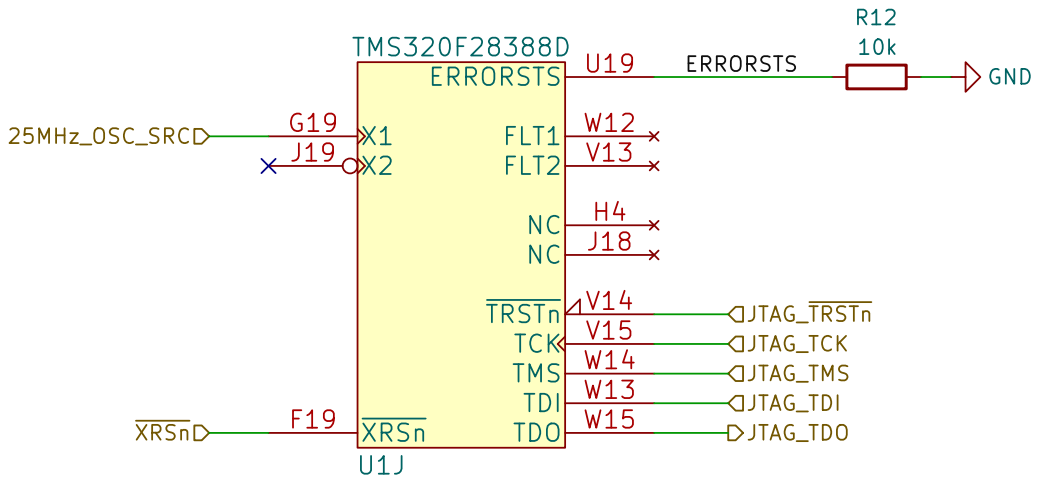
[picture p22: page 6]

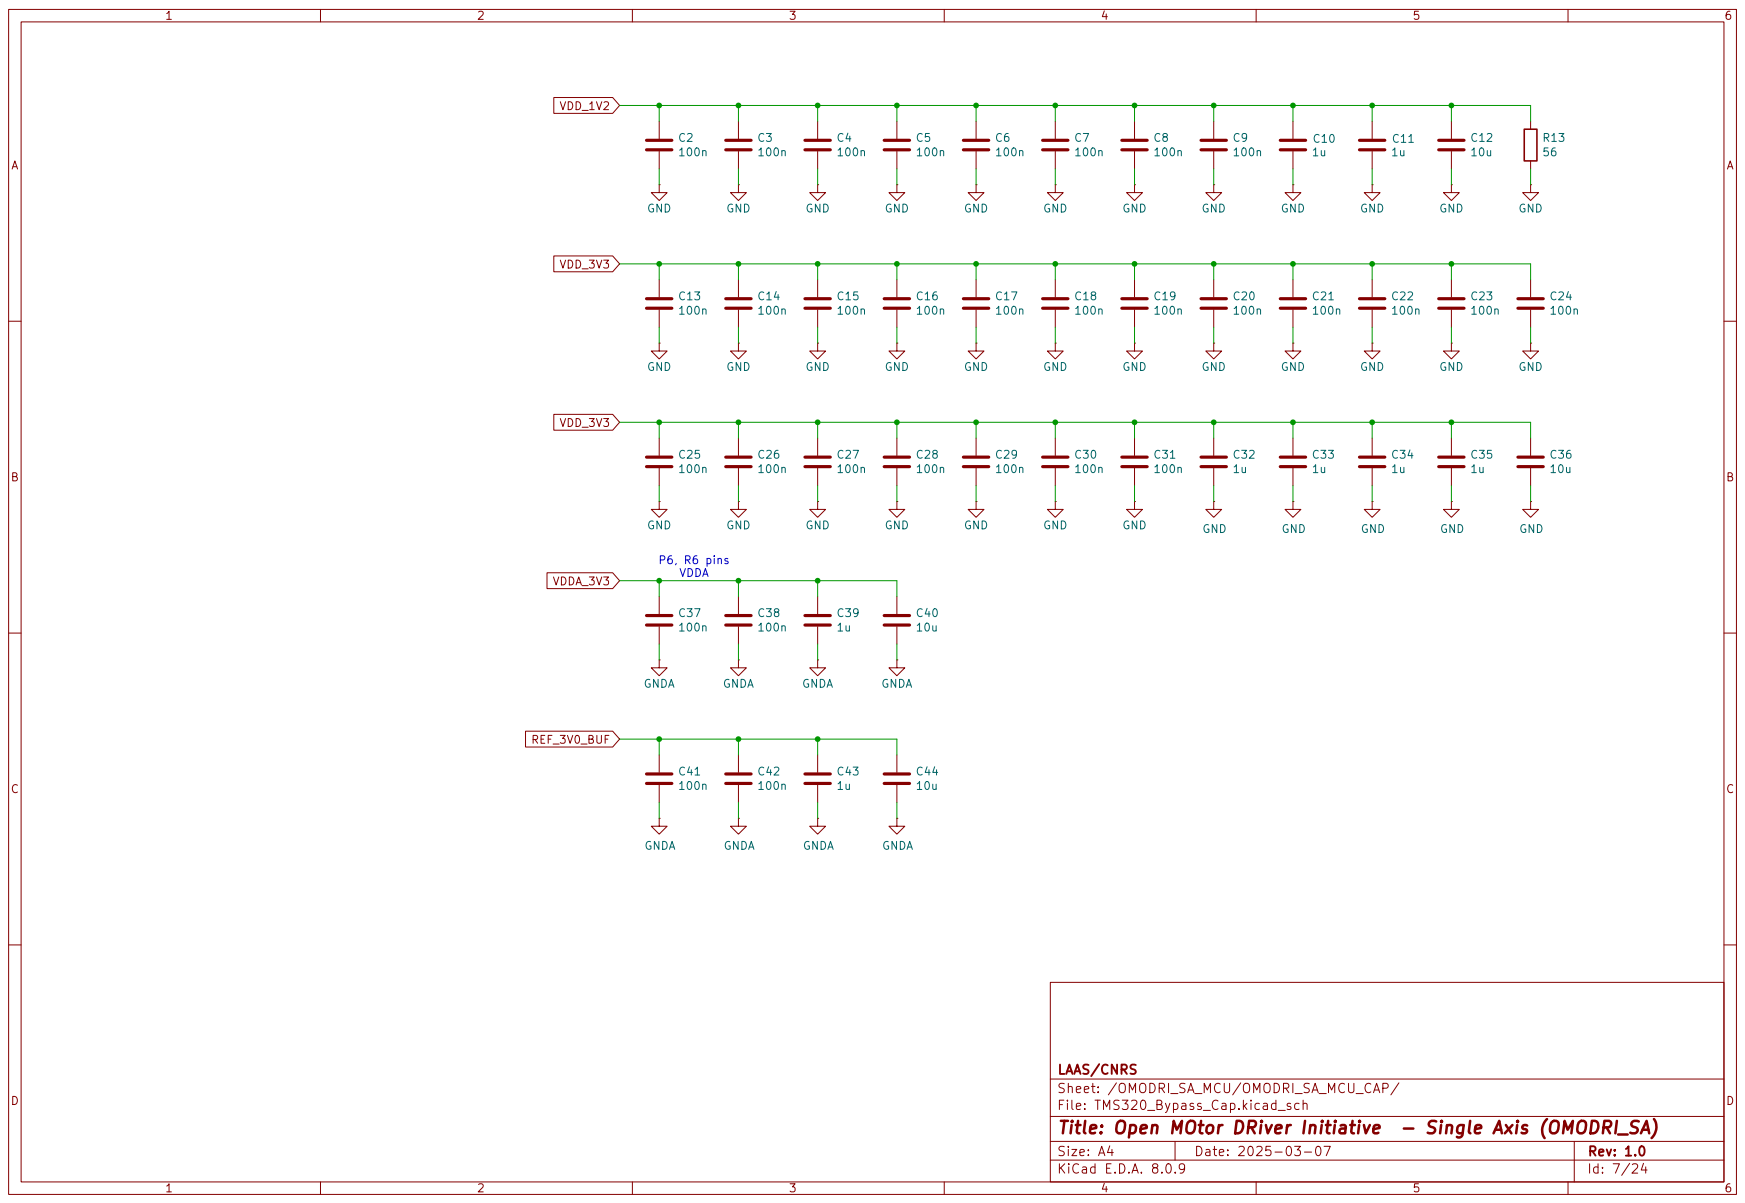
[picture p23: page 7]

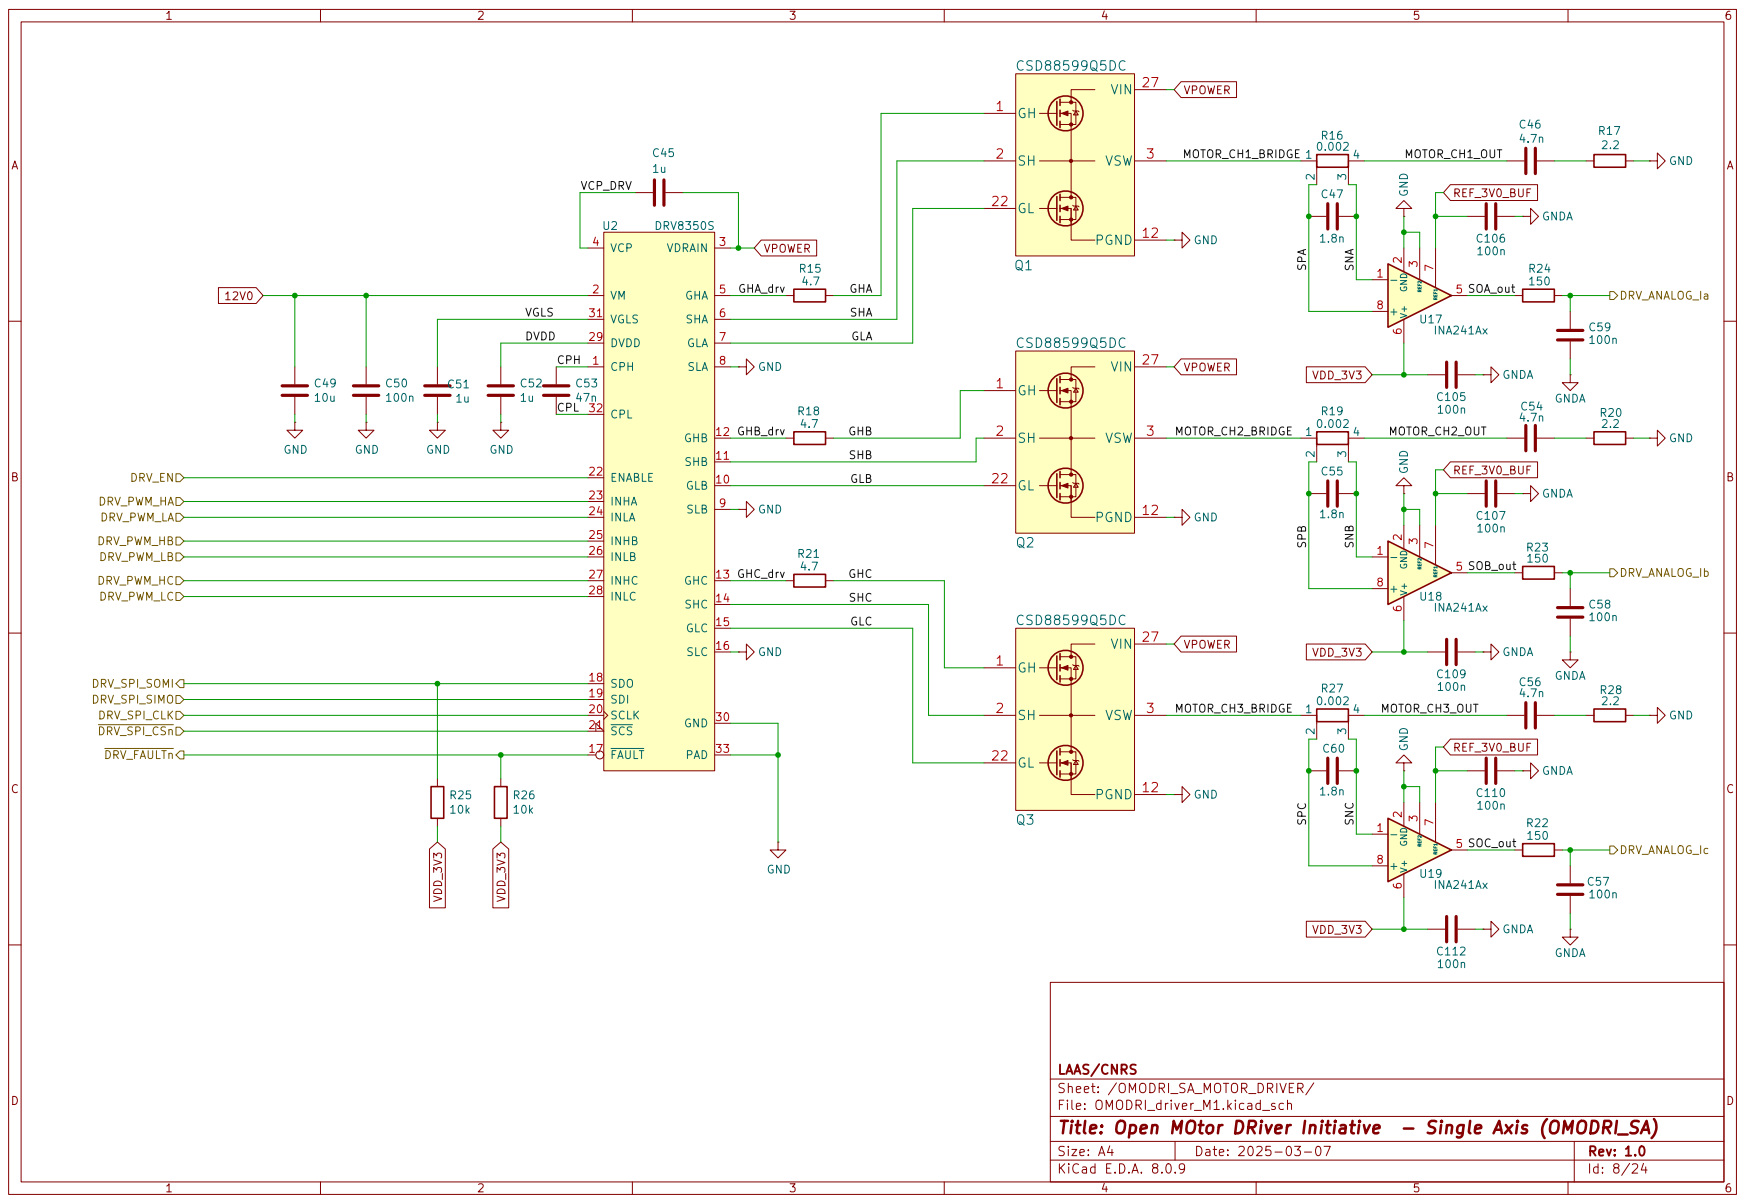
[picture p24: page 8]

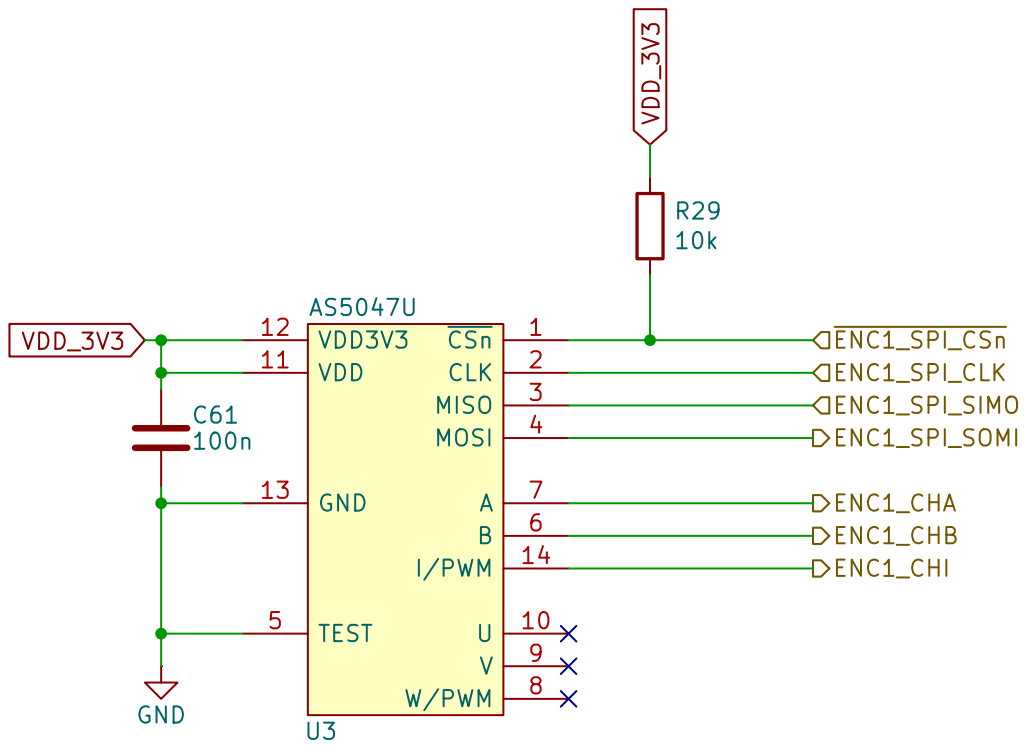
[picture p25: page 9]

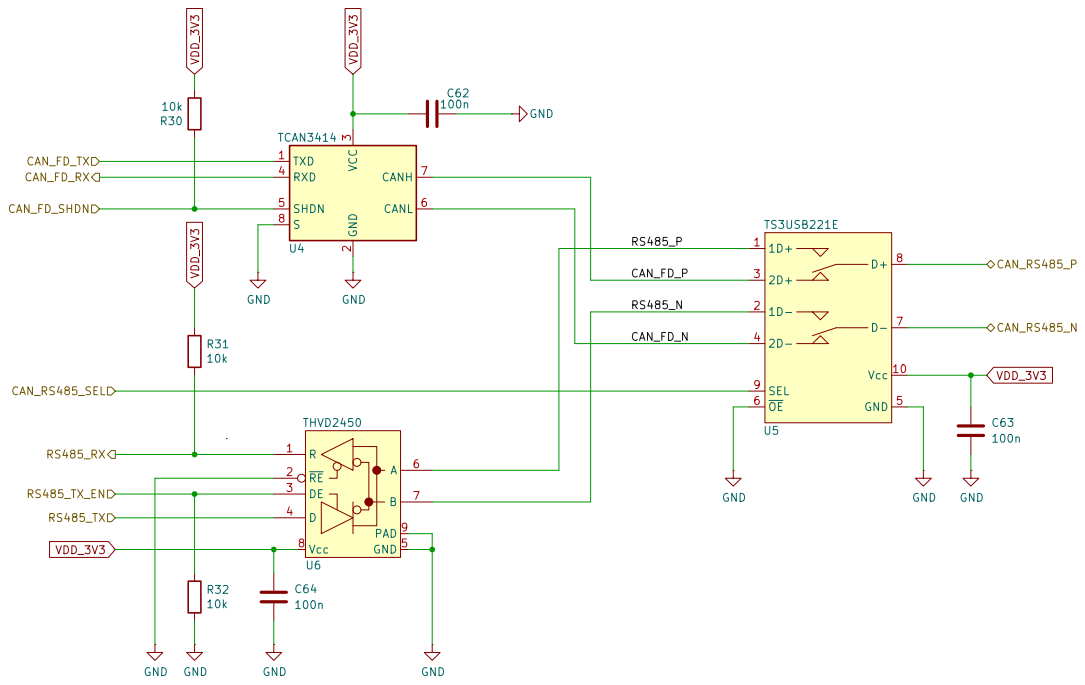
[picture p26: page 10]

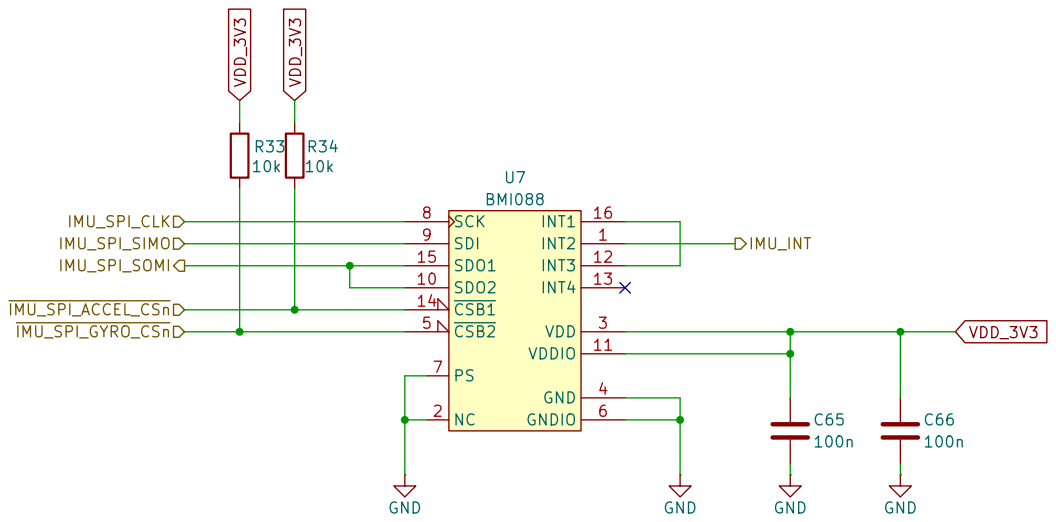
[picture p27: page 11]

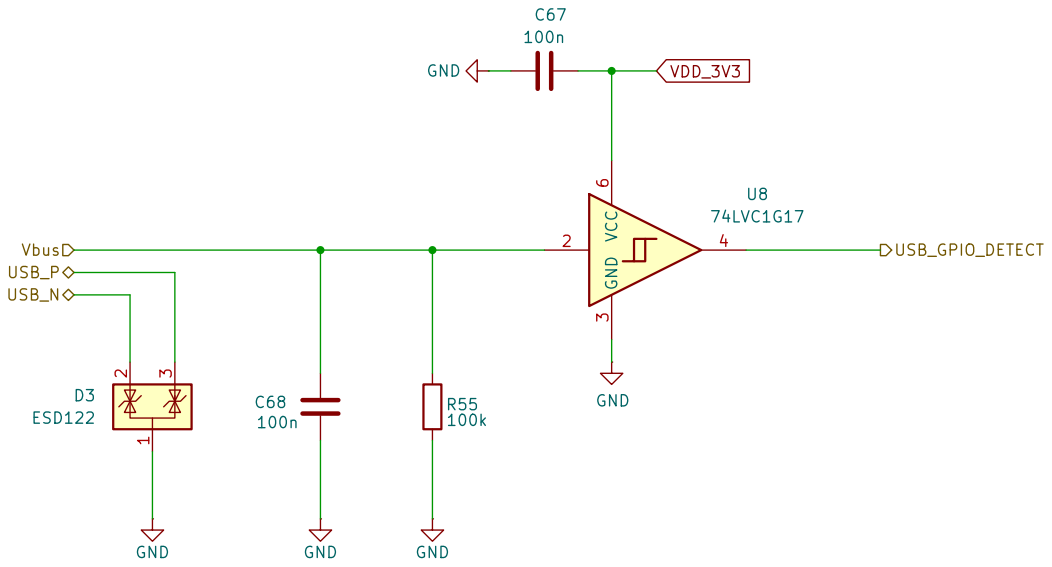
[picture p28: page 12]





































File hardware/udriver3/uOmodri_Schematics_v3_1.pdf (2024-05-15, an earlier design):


conn_01x04_MountingPins C2
6.028 kHz anti aliasing GNDA R6

Id: 1/22 Title: Open MOtor DRiver Initiative (OMODRI) File: omodri_laas.kicad_sch Sheet: / LAAS/CNRS



Id: 3/22 Title: Open MOtor DRiver Initiative (OMODRI) File: OMODRI_FSI_TX.kicad_sch Sheet: /OMODRI_FSI_TX/ LAAS/CNRS


Id: 4/22 Title: Open MOtor DRiver Initiative (OMODRI) File: OMODRI_FSI_RX.kicad_sch Sheet: /OMODRI_FSI_RX/ LAAS/CNRS


3 RXD 4 SHDN 5 CANL 6 CANH 7 S

Id: 5/22 Title: Open MOtor DRiver Initiative (OMODRI) File: OMODRI_CAN_RS845.kicad_sch Sheet: /OMODRI_CAN_RS485/ LAAS/CNRS


Id: 6/22 Title: Open MOtor DRiver Initiative (OMODRI) File: OMODRI_LED_dbg.kicad_sch Sheet: /OMODRI_LED_dbg/ LAAS/CNRS


Id: 7/22 Title: Open MOtor DRiver Initiative (OMODRI) File: OMODRI_POWER_CAP.kicad_sch Sheet: /OMODRI_POWER_CAP/ LAAS/CNRS


2 OUT 3 Vdd 4 X1 ECS-TXO-2016 GND


Id: 9/22 Title: Open MOtor DRiver Initiative (OMODRI) File: OMODRI_GPIO.kicad_sch Sheet: /OMODRI_GPIO/ LAAS/CNRS


Id: 10/22 Title: Open MOtor DRiver Initiative (OMODRI) File: OMODRI_ANALOG.kicad_sch Sheet: /OMODRI_GPIO/OMODRI_ANALOG/ LAAS/CNRS


Id: 11/22 Title: Open MOtor DRiver Initiative (OMODRI) File: OMODRI_ETHERCAT_CONNECT.kicad_sch Sheet: /OMODRI_GPIO/OMODRI_ETHERCAT_CONNECT/ LAAS/CNRS


Id: 12/22 Title: Open MOtor DRiver Initiative (OMODRI) File: OMODRI_driver_M1.kicad_sch Sheet: /OMODRI_driver_M1/ LAAS/CNRS


SHA GHA Note, make sure to choose low esr for C92, same for motor 1.. C41









Id: 21/22 Title: Open MOtor DRiver Initiative (OMODRI) File: OMODRI_IMU_DBG.kicad_sch Sheet: /OMODRI_IMU_DBG/ LAAS/CNRS


Id: 22/22 Title: Open MOtor DRiver Initiative (OMODRI) File: OMODRI_COM_SPI_USB.kicad_sch Sheet: /OMODRI_COM_SPI_USB/ LAAS/CNRS

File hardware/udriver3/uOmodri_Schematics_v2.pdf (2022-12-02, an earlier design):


File: omodri_laas.kicad_sch Sheet: / LAAS/CNRS

Id: 1/22 Title: Open MOtor DRiver Initiative (OMODRI)


AEDT-981x encoders output are push-pull so we can remove the pull up, or at least make it optional, not sure about the need for the capacitors

5 MP1 MP2 2 ENC1_B

File: OMODRI_QuadEncod.kicad_sch
Id: 2/22 Title: Open MOtor DRiver Initiative (OMODRI)


5 NC 6 NC 7 D6 8 D5 9 D1 TPD6E05U06 EN 1 DOUT4+ 10 DOUT3+ 11 DOUT3- 12 DOUT2- 13 DOUT2+ 14 DOUT1+ 15 DOUT1- 16 DIN1 2 DIN2 3 VCC 4 GND 5 DIN3 6 DIN4 7 ~{EN_n} 8 DOUT4- 9 U4 DSLVDS1047

File: OMODRI_FSI_TX.kicad_sch
Id: 3/22 Title: Open MOtor DRiver Initiative (OMODRI)


5 NC 6 NC 7 D6 8 D5 9 D3TPD6E05U06 GND GND GND 1

File: OMODRI_FSI_RX.kicad_sch
Id: 4/22 Title: Open MOtor DRiver Initiative (OMODRI)


File: OMODRI_LED_dbg.kicad_sch
Id: 6/22 Title: Open MOtor DRiver Initiative (OMODRI)


File: OMODRI_POWER_CAP.kicad_sch
Id: 7/22 Title: Open MOtor DRiver Initiative (OMODRI)


2 OUT 3 Vdd 4 X1 ECS-TXO-2016 R26

File: OMODRI_JTAG_OSC_RST.kicad_sch Sheet: /JTAG + CLOCK + RESET/ LAAS/CNRS

Id: 8/22 Title: Open MOtor DRiver Initiative (OMODRI)


File: OMODRI_GPIO.kicad_sch
Id: 9/22 Title: Open MOtor DRiver Initiative (OMODRI)


2 D8TPD1E04U04 GND VREFLOC P2 ADCINC3 P3 ADCINC5 P4 VREFHIC R1 VREFLOA R2 ADCINC2 R3 ADCINC4 R4 ADCINA1 T1 ADCINA3 T2 ADCINA5 T3 ADCIN14 T4 ADCIND0 T5 ADCIND2 T6 ADCIND4 T7 ADCINA0 U1 ADCINA2 U2 ADCINA4 U3 ADCIN15 U4 ADCIND1 U5 ADCIND3 U6 ADCIND5 U7 VREFHIA V1 ADCINB0 V2 ADCINB2 V3 ADCINB4 V4 VREFHID V5 VREFLOB V6 ADCINB1 W2 ADCINB3 W3 ADCINB5 W4 VREFHIB W5 VREFLOD W6 U6C
TMS320F28388D

File: OMODRI_ANALOG.kicad_sch
Id: 10/22 Title: Open MOtor DRiver Initiative (OMODRI)


File: OMODRI_ETHERCAT_CONNECT.kicad_sch
Id: 11/22 Title: Open MOtor DRiver Initiative (OMODRI)


VGLS

~{nFAULT} SDI ~{nSCS} SCLK

File: OMODRI_driver_M1.kicad_sch
Id: 12/22 Title: Open MOtor DRiver Initiative (OMODRI)


File: OMODRI_driver_M2.kicad_sch
Id: 13/22 Title: Open MOtor DRiver Initiative (OMODRI)


File: OMODRI_power.kicad_sch Sheet: /Power distribution/ LAAS/CNRS

Id: 14/22 Title: Open MOtor DRiver Initiative (OMODRI)


U11.5 : DNC - Do not connect. Do not connect this pin to ground, to another pin, or to any other voltage. This pin is
connected to the internal bootstrap capacitor. This pin must be soldered to an isolated pad.
U11.3, U11.6, U11.13 : NC - these pins to the PGND plane can help enhance shielding and thermal performance.
U11.12 : PGOOD - A 10-kohm to 100-kohm pullup resistor is required and can be tied to the V5V pin or other DC voltage less than 18V. ---------------------------------------- R48 = 10kohm (recommended)

R50 = 2.49kohm (R50 = R48 / (5V - 1))
---------------------------------------- Cin > 9.4uF C56 + C57 + C58 = (10uF + 10uF + 100nF) rated @ 75V. ---------------------------------------- Cout > 15uF (according figure 7-2 in datasheet SLVSG72 / TPSM560R6H) C59 = 22uF/25V

Sheet: /Power distribution/OMODRI_Alim_5V/ LAAS/CNRS

File: OMODRI_Alim_5V.kicad_sch
Id: 15/22 Title: Open MOtor DRiver Initiative (OMODRI)


Sheet: /Power distribution/OMODRI_Alim_3V3/ LAAS/CNRS

File: OMODRI_Alim_3V3.kicad_sch
Id: 16/22 Title: Open MOtor DRiver Initiative (OMODRI)


Sheet: /Power distribution/OMODRI_Alim_1V2/ LAAS/CNRS

File: OMODRI_Alim_1V2.kicad_sch
Id: 17/22 Title: Open MOtor DRiver Initiative (OMODRI)


Sheet: /Power distribution/OMODRI_Alim_REF/ LAAS/CNRS

File: OMODRI_Alim_REF.kicad_sch
Id: 18/22 Title: Open MOtor DRiver Initiative (OMODRI)


Sheet: /Power distribution/TMS320_Bypass_Cap/ LAAS/CNRS

File: TMS320_Bypass_Cap.kicad_sch
Id: 19/22 Title: Open MOtor DRiver Initiative (OMODRI)

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


































































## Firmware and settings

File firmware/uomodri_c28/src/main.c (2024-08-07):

/*
 * File name: main.c
 * Description: Source file containing main function and IT running on CPU1 - C28 processor.
 */

/***********************************************************************
 * INCLUDES
 ***********************************************************************/
#include "driverlib.h"
#include "device.h"
#include "board.h"

#include "uomodri_user_defines.h"
#include "config/uomodri_math.h"

#if (USE_UOMODRI_REV == USE_UOMODRI_V2)
#include "config/uomodri_2/uomodri_2_handlers.h"    // uOmodri v2.x configuration include file
#elif (USE_UOMODRI_REV == USE_UOMODRI_V3)
#include "config/uomodri_3/uomodri_3_handlers.h"    // uOmodri v3.x configuration include file
#endif

#include "communication.h"
#include "motor_ctrl.h"
#include "drv8353.h"
#include "ws2812b.h"
#include "main.h"
#include "hal.h"

/***********************************************************************
 * FUNCTIONS DECLARATION
 ***********************************************************************/
void main(void);
static void MCU_ini(void);
inline void LED_dimming(motor_t*, motor_t*, uint16_t*);
void MOT_initStruct(motor_t*, uint16_t);

__attribute__((interrupt)) void cla_isrClearTask(void);
__attribute__((interrupt)) void cla_isrMotor1(void);
__attribute__((interrupt)) void cla_isrMotor2(void);
__attribute__((interrupt)) void tmr_isrLedCmd(void);
__attribute__((interrupt)) void dma_isrSpiComRx(void);
__attribute__((interrupt)) void sci_isrTx_RS485(void);
__attribute__((interrupt)) void sci_isrRx_RS485(void);
__attribute__((interrupt)) void clb_isrTxRx_RS485(void);
__attribute__((interrupt)) void errata_isr(void);

/***********************************************************************
 * VARIABLES
 ***********************************************************************/
/** @var    int_cfg_t   interruptList[]
 *  @brief  List all required interrupts configurations.
 */
static const int_cfg_t interruptList[] =
{
 INT_ERRATA_DEF,
 INT_CLA_ADC_CALIB_DEF,
 INT_CLA_MOTOR1_DEF,
 INT_CLA_MOTOR2_DEF,
 INT_TIMER_LED_DEF,
 INT_DMA_RX_MSG_DEF,
#if (RS485_BUS_ENABLE) && (USE_UOMODRI_REV != USE_UOMODRI_V1)
 INT_RS485_TX_MSG_DEF,
 INT_RS485_RX_MSG_DEF,
 INT_RS485_Rx_Tx_CLB_DEF,
#endif
 {.intNum = UINT32_MAX},        /* END OF ARRAY */
};

#pragma DATA_ALIGN(motor_m1, 4)
#pragma DATA_SECTION(motor_m1, "ClaDataMotor1");
motor_t     motor_m1;

#pragma DATA_ALIGN(motor_m2, 4)
#pragma DATA_SECTION(motor_m2, "ClaDataMotor2");
motor_t     motor_m2;

#pragma DATA_ALIGN(cmd_uomodri, 4)
#pragma DATA_SECTION(cmd_uomodri, "MSGRAM_CPU_TO_CLA")
cmd_t       cmd_uomodri[2];

#pragma DATA_ALIGN(com_spi_rx, 4)
#pragma DATA_SECTION(com_spi_rx, "ramgs0")
spi_rx_t    com_spi_rx;

#pragma DATA_ALIGN(com_spi_tx, 4)
#pragma DATA_SECTION(com_spi_tx, "ramgs0")
spi_tx_t    com_spi_tx      = {.msg_cr = 0U, .msg_nx = 1U,
                               .msg[0].crc.u16_msb = 0xDFFF, .msg[0].crc.u16_lsb = 0x5283,
                               .msg[1].crc.u16_msb = 0xDFFF, .msg[1].crc.u16_lsb = 0x5283};
#pragma DATA_ALIGN(com_rs485_rx, 4)
#pragma DATA_SECTION(com_rs485_rx, "ramgs0")
rs485_rx_t  com_rs485_rx    = {.index = 0U,
                               .addr1 = false, .addr2 = false};

#pragma DATA_ALIGN(com_rs485_tx, 4)
#pragma DATA_SECTION(com_rs485_tx, "ramgs0")
rs485_tx_t  com_rs485_tx    = {.index = 0U,
                               .msg_cr = 0U, .msg_nx = 1U,
                               .msg[0].crc.u16_msb = 0x8CA0, .msg[0].crc.u16_lsb = 0x22CF,
                               .msg[1].crc.u16_msb = 0x8CA0, .msg[1].crc.u16_lsb = 0x22CF};

#pragma DATA_ALIGN(led_spi_tx, 4)
#pragma DATA_SECTION(led_spi_tx, "ramgs0")
uint16_t    led_spi_tx[LED_MSG_TX_16BIT_LENGTH];

#pragma DATA_ALIGN(com_bus_select, 2)
#pragma DATA_SECTION(com_bus_select, "ramgs0")
com_bus_e   com_bus_select      = COM_NO_BUS_DEFINED;

#pragma DATA_ALIGN(global_1ms_tmr_cnt, 2)
#pragma DATA_SECTION(global_1ms_tmr_cnt, "ramgs0")
uint32_t    global_1ms_tmr_cnt  = 0U;

#pragma DATA_ALIGN(global_errata_cnt, 2)
#pragma DATA_SECTION(global_errata_cnt, "ramgs0")
uint32_t    global_errata_cnt   = 0U;

/***********************************************************************
 * EXTERNAL VARIABLES
 ***********************************************************************/
extern const hal_cfg_t  hal;

/***********************************************************************
 * FUNCTIONS DEFINITION
 ***********************************************************************/
/**
 * @brief   	Main function running on CPU1/C28.
 *              - MCU init,
 *              - motors structures init,
 *              - communication structure init,
 *              - MCU peripherals init,
 *              - DRV init,
 *              - ADC task calibration,
 *              - IT init.
 */
void main(void)
{
    // uOmodri low level device initialization
    MCU_ini();
    // Initialization of the shared structure used by CLA & C28 for Motor_1 & Motor_2
    MOT_initStruct(&motor_m1, MOTOR_1);
    MOT_initStruct(&motor_m2, MOTOR_2);
    // Initialization the command structure for CLA.
    COM_initCmdStruct(&cmd_uomodri[MOTOR_1]);
    COM_initCmdStruct(&cmd_uomodri[MOTOR_2]);
    // Hardware Abstraction Layer initialization
    HAL_ini(&hal);
    // DRV8353 initialization
    cmd_uomodri[MOTOR_1].periphField.drv_initErr = DRV_ini(&drv_cfg[MOTOR_1], &drv_reg[MOTOR_1]);
    cmd_uomodri[MOTOR_2].periphField.drv_initErr = DRV_ini(&drv_cfg[MOTOR_2], &drv_reg[MOTOR_2]);
    // Start ADC offset calibration on CLA
    CLA_forceTasks(CLA1_BASE, CLA_ADC_CALIB_TASK_FLAG);
    // Interrupts initialization
    HAL_INT_ini(interruptList);
//    // SPI check parameters
//    if((COM_MSG_SPI_TX_16BIT_PAYLOAD_LENGTH != COM_MSG_SPI_RX_16BIT_PAYLOAD_LENGTH) || \
//            (COM_MSG_SPI_TX_16BIT_FULL_LENGTH != COM_MSG_SPI_RX_16BIT_FULL_LENGTH))
//    error "Error : SPI Tx & Rx must have the same length."

    // Infinite loop
    while(1);
}

/**
 * @brief       Microcontroller initialization function
 *                  - Configure master clock to 200MHz
 *                  - Configure auxiliary clock (CM core) to 125MHz (USB � 60MHz)
 *                  - Enable GPIO clocking
 *                  - Configure the interruption vector table
 *                  - Boot CM from flash or RAM
 */
static void MCU_ini(void)
{
    /* Initialize clock and peripherals */
    Device_init();

    /*
     * LSPCLK redefine - SPIx Bit Clock & SCIx Bit Clock.
     * DEVICE_SYSCLK_FREQ (200MHz) instead of DEVICE_SYSCLK_FREQ / 4 (50MHz)
     */
#if (UOMODRI_LSPCLK_FREQ == DEVICE_SYSCLK_FREQ)
    SysCtl_setLowSpeedClock(SYSCTL_LSPCLK_PRESCALE_1);
#ifdef DEBUG
    ASSERT(SysCtl_getLowSpeedClock(DEVICE_OSCSRC_FREQ) == UOMODRI_LSPCLK_FREQ);
#endif /* DEBUG */
#endif

    /*
     * SYSCLK to EPWMCLK DIVIDER define - ePWM peripheral & CLB tiles.
     * EPWMCLK_FREQ (100MHz) = DEVICE_SYSCLK_FREQ (200MHz) / PLLSYSCLK_TO_EPWMCLK_DIV (2)
     */
    SysCtl_setEPWMClockDivider(PLLSYSCLK_TO_EPWMCLK_DIV);

    /* Set the CLB/tile clock */
#if (CLB_TILE_ENABLE)
    /*
     * Use SYSCLK / PERCLKDIVSEL.EPWMCLKDIV (2) as Tile clock (100MHz).
     */

    /* Redefined to pass to SysCtl_setAuxClock(). Will configure the clock as follows:
     * AUXPLLCLK = 25MHz (XTAL_OSC) * 48 (IMULT) / (2 (REFDIV) * 5 (ODIV) * 2(AUXPLLDIV) )
     * AUXPLLCLK require a 60MHz clock for USB. AUPLLRAWCLK require a 120MHz clock for CM. */
//#undef DEVICE_AUXSETCLOCK_CFG
//#define DEVICE_AUXSETCLOCK_CFG      (SYSCTL_AUXPLL_OSCSRC_XTAL  | \
                                     SYSCTL_AUXPLL_IMULT(48)    | \
                                     SYSCTL_AUXPLL_REFDIV(2U)   | \
                                     SYSCTL_AUXPLL_ODIV(5U)     | \
                                     SYSCTL_AUXPLL_DIV_2        | \
                                     SYSCTL_AUXPLL_ENABLE       | \
                                     SYSCTL_DCC_BASE_0)
//#undef DEVICE_AUXCLK_FREQ
//#define DEVICE_AUXCLK_FREQ          ((DEVICE_OSCSRC_FREQ * 48) / (2 * 5 * 2))
#endif

#if (defined USB_BUS_ENABLE_ON_CM) && (!defined CPU1)
    /* Allocate Shared Peripheral USB to the CM Side. */
    SysCtl_allocateSharedPeripheral(SYSCTL_PALLOCATE_USBA, 1);
#endif
    /* Boot CM core */
#if (defined _FLASH) && (!defined CPU1)
    Device_bootCM(BOOTMODE_BOOT_TO_FLASH_SECTOR0);
#elif (!defined CPU1)
    Device_bootCM(BOOTMODE_BOOT_TO_S0RAM);
#endif
    // Initialize GPIO
    Device_initGPIO();
    /* Initializes PIE and clears PIE registers. Disables CPU interrupts. */
    Interrupt_initModule();
    /* Initialize the PIE vector table with pointers to the shell Interrupt Service Routines (ISR). */
    Interrupt_initVectorTable();

    return;
}

/**
 * @brief       Control the led dimming
 * @param[in]   p_motor Pointer on data structure array used for motor control.
 * @param[out]  p_msg   Pointer on the message to be sent to led via SPI.
 */
inline void LED_dimming(motor_t* p_motor1, motor_t* p_motor2, uint16_t* p_msg)
{
    static uint16_t timer_cpt_ms    = 0;
//    uint16_t        i               = 0;
    motor_state_e   motor_state     = MOTOR_STATE_IDLE;

    /* Set status of the 1st led */
    if((p_motor1->state & MOTOR_STATE_BOOT)     || (p_motor2->state & MOTOR_STATE_BOOT))
        motor_state = MOTOR_STATE_IDLE;
    else if((p_motor1->state & MOTOR_STATE_INIT)|| (p_motor2->state & MOTOR_STATE_INIT))
        motor_state = MOTOR_STATE_INIT_FIX;
    else if((p_motor1->state & MOTOR_STATE_OK)  || (p_motor2->state & MOTOR_STATE_OK))
        motor_state = MOTOR_STATE_READY;
    if((p_motor1->state == MOTOR_STATE_ERROR)   || (p_motor2->state == MOTOR_STATE_ERROR))
        motor_state = MOTOR_STATE_ERROR;

    // Master LED (1st led)
    p_msg       = ws2812b_dimmingLed(MASTER_LED, motor_state, timer_cpt_ms, p_msg);
    //MOTOR_1 LED (2nd led)
    p_msg       = ws2812b_dimmingLed(MOTOR1_LED, p_motor1->state, timer_cpt_ms, p_msg);
    //MOTOR_2 LED (3th led)
    p_msg       = ws2812b_dimmingLed(MOTOR2_LED, p_motor2->state, timer_cpt_ms, p_msg);
    // millisecond timer increment
    timer_cpt_ms= (timer_cpt_ms < 1000U) ? (timer_cpt_ms + 1): (0U);

    return;
}

/**
 * @brief       Global structure initialization for MOTOR_1 \& MOTOR_2
 * @param[in]   *p_motor    Pointer on the associated motor structure
 * @param[in]   motor_id    Motor identifier.
 */
void MOT_initStruct(motor_t* p_motor, uint16_t motor_id)
{
    if(motor_id == MOTOR_1)
    {
        //--- MOTOR_1 -----------------------------------------------------------
        p_motor->id                                     = MOTOR_1;
        //--- FOC structure -----------------------------------------------------
        //--- MOTOR PARAMS STRUCTURE --------------------------------------------
        p_motor->foc.cfg.Rs                             = MOTOR1_RS;
        p_motor->foc.cfg.Ls                             = MOTOR1_LS;
        p_motor->foc.cfg.kv                             = MOTOR1_KV;
        p_motor->foc.cfg.ke                             = MOTOR1_KE;
        p_motor->foc.cfg.ki                             = MOTOR1_KI;
        p_motor->foc.cfg.polePairs                      = MOTOR1_POLES_PAIRS;
        //--- MOTOR ACQUISITION STRUCTURE ---------------------------------------
        p_motor->foc.acq.iabcCfgBase[CHANNEL_1]         = MOTOR1_IA_ADC_CFG_ADDR;
        p_motor->foc.acq.iabcCfgBase[CHANNEL_2]         = MOTOR1_IB_ADC_CFG_ADDR;
        p_motor->foc.acq.iabcCfgBase[CHANNEL_3]         = MOTOR1_IC_ADC_CFG_ADDR;
        p_motor->foc.acq.iabcResultBase[CHANNEL_1]      = MOTOR1_IA_ADC_RESULT_ADDR;
        p_motor->foc.acq.iabcResultBase[CHANNEL_2]      = MOTOR1_IB_ADC_RESULT_ADDR;
        p_motor->foc.acq.iabcResultBase[CHANNEL_3]      = MOTOR1_IC_ADC_RESULT_ADDR;
        p_motor->foc.acq.vExtResultBase                 = VEXT1_ADC_RESULT_ADDR;
        p_motor->foc.acq.ppbNum.ia                      = MOTOR1_IABC_PPB_NUM;
        p_motor->foc.acq.ppbNum.ib                      = MOTOR1_IABC_PPB_NUM;
        p_motor->foc.acq.ppbNum.ic                      = MOTOR1_IABC_PPB_NUM;
        p_motor->foc.acq.ppbNum.vExt                    = VEXT1_PPB_NUM;
        p_motor->foc.acq.socNum.ia                      = MOTOR1_IABC_SOC_NUM;
        p_motor->foc.acq.socNum.ib                      = MOTOR1_IABC_SOC_NUM;
        p_motor->foc.acq.socNum.ic                      = MOTOR1_IABC_SOC_NUM;
        p_motor->foc.acq.socNum.vExt                    = VEXT1_SOC_NUM;
        p_motor->foc.acq.intNum.adcInt                  = MOTOR1_IA_INT_NUM;
        //--- MOTOR ENCORDER STRUCTURE ------------------------------------------
        p_motor->foc.enc.eqepBase                       = MOTOR1_QEP_BASE;
        p_motor->foc.enc.polePairs                      = MOTOR1_POLES_PAIRS;
        p_motor->foc.enc.thetaMechScaler                = (float32_t)MOTOR1_ENC_RESOLUTION_SCALE;
        p_motor->foc.enc.speed.speedHighScaler          = (float32_t)MOTOR1_ENC_SPEED_HIGH_SCALE;
        p_motor->foc.enc.speed.speedLowScaler           = (float32_t)MOTOR1_ENC_SPEED_LOW_SCALE;
        p_motor->foc.enc.speed.speedFlt[0].a            = (float32_t)MOTOR1_ENC_SPEED_LPF_ALPHA;
        p_motor->foc.enc.speed.speedFlt[0].one_minus_a  = (float32_t)MOTOR1_ENC_SPEED_LPF_ONE_M_ALPHA;
        p_motor->foc.enc.speed.speedFlt[1].a            = (float32_t)MOTOR1_ENC_SPEED_LOCAL_LPF_ALPHA;
        p_motor->foc.enc.speed.speedFlt[1].one_minus_a  = (float32_t)MOTOR1_ENC_SPEED_LOCAL_LPF_ONE_M_ALPHA;
        //--- MOTOR COMMAND STRUCTURE -------------------------------------------
        p_motor->foc.cmd.iSat                           = MOTOR1_CURRENT_CMD_SAT_MAX;
        //-----------------------------------------------------------------------
        p_motor->foc.iParkFlt.a                         = MOTOR1_CURRENT_LPF_ALPHA;
        p_motor->foc.iParkFlt.one_minus_a               = MOTOR1_CURRENT_LPF_ONE_M_ALPHA;
        //--- FOC - Initialize duty cycle saturation ----------------------------
        p_motor->foc.dtcMax                             = MOTOR1_DTC_MAX;
        p_motor->foc.dtcMin                             = MOTOR1_DTC_MIN;
        //--- FOC - Encoder test ------------------------------------------------
        p_motor->foc.initPosCnt                         = MOTOR1_POSITION_INIT_EVT;
        p_motor->foc.initFixCnt                         = MOTOR1_FIX_INIT_EVT;
        p_motor->foc.initErr[MIN]                       = MOTOR1_POSITION_INIT_ERR_MIN;
        p_motor->foc.initErr[MAX]                       = MOTOR1_POSITION_INIT_ERR_MAX;
        //--- FOC - Initialize PI controller (Id) -------------------------------
        p_motor->foc.piId.kp                            = (float32_t)MOTOR1_PI_ID_KP_COEF;
        p_motor->foc.piId.ki                            = (float32_t)MOTOR1_PI_ID_KI_COEF;
        //--- FOC - Initialize PI controller (Iq) -------------------------------
        p_motor->foc.piIq.kp                            = (float32_t)MOTOR1_PI_IQ_KP_COEF;
        p_motor->foc.piIq.ki                            = (float32_t)MOTOR1_PI_IQ_KI_COEF;
        //--- DRV IO Config -----------------------------------------------------
        p_motor->drvFaultNum                            = MOTOR1_DRV_FAULT_NUM;
        p_motor->drvEnNum                               = MOTOR1_DRV_EN_NUM;
        //---- PWM config address -----------------------------------------------
        p_motor->epwmBase[CHANNEL_1]                    = MOTOR1_PWM1_BASE;
        p_motor->epwmBase[CHANNEL_2]                    = MOTOR1_PWM2_BASE;
        p_motor->epwmBase[CHANNEL_3]                    = MOTOR1_PWM3_BASE;
    }
    else
    {
        //--- MOTOR_2 -----------------------------------------------------------
        p_motor->id                                     = MOTOR_2;
        //--- FOC structure -----------------------------------------------------
        //--- MOTOR PARAMS STRUCTURE --------------------------------------------
        p_motor->foc.cfg.Rs                             = MOTOR2_RS;
        p_motor->foc.cfg.Ls                             = MOTOR2_LS;
        p_motor->foc.cfg.kv                             = MOTOR2_KV;
        p_motor->foc.cfg.ke                             = MOTOR2_KE;
        p_motor->foc.cfg.ki                             = MOTOR2_KI;
        p_motor->foc.cfg.polePairs                      = MOTOR2_POLES_PAIRS;
        //--- MOTOR ACQUISITION STRUCTURE ---------------------------------------
        p_motor->foc.acq.iabcCfgBase[CHANNEL_1]         = MOTOR2_IA_ADC_CFG_ADDR;
        p_motor->foc.acq.iabcCfgBase[CHANNEL_2]         = MOTOR2_IB_ADC_CFG_ADDR;
        p_motor->foc.acq.iabcCfgBase[CHANNEL_3]         = MOTOR2_IC_ADC_CFG_ADDR;
        p_motor->foc.acq.iabcResultBase[CHANNEL_1]      = MOTOR2_IA_ADC_RESULT_ADDR;
        p_motor->foc.acq.iabcResultBase[CHANNEL_2]      = MOTOR2_IB_ADC_RESULT_ADDR;
        p_motor->foc.acq.iabcResultBase[CHANNEL_3]      = MOTOR2_IC_ADC_RESULT_ADDR;
        p_motor->foc.acq.vExtResultBase                 = VEXT2_ADC_RESULT_ADDR;
        p_motor->foc.acq.ppbNum.ia                      = MOTOR2_IABC_PPB_NUM;
        p_motor->foc.acq.ppbNum.ib                      = MOTOR2_IABC_PPB_NUM;
        p_motor->foc.acq.ppbNum.ic                      = MOTOR2_IABC_PPB_NUM;
        p_motor->foc.acq.ppbNum.vExt                    = VEXT2_PPB_NUM;
        p_motor->foc.acq.socNum.ia                      = MOTOR2_IABC_SOC_NUM;
        p_motor->foc.acq.socNum.ib                      = MOTOR2_IABC_SOC_NUM;
        p_motor->foc.acq.socNum.ic                      = MOTOR2_IABC_SOC_NUM;
        p_motor->foc.acq.socNum.vExt                    = VEXT2_SOC_NUM;
        p_motor->foc.acq.intNum.adcInt                  = MOTOR2_IA_INT_NUM;
        //--- MOTOR ENCORDER STRUCTURE ------------------------------------------
        p_motor->foc.enc.eqepBase                       = MOTOR2_QEP_BASE;
        p_motor->foc.enc.polePairs                      = MOTOR2_POLES_PAIRS;
        p_motor->foc.enc.thetaMechScaler                = (float32_t)MOTOR2_ENC_RESOLUTION_SCALE;
        p_motor->foc.enc.speed.speedHighScaler          = (float32_t)MOTOR2_ENC_SPEED_HIGH_SCALE;
        p_motor->foc.enc.speed.speedLowScaler           = (float32_t)MOTOR2_ENC_SPEED_LOW_SCALE;
        p_motor->foc.enc.speed.speedFlt[0].a            = (float32_t)MOTOR2_ENC_SPEED_LPF_ALPHA;
        p_motor->foc.enc.speed.speedFlt[0].one_minus_a  = (float32_t)MOTOR2_ENC_SPEED_LPF_ONE_M_ALPHA;
        p_motor->foc.enc.speed.speedFlt[1].a            = (float32_t)MOTOR2_ENC_SPEED_LOCAL_LPF_ALPHA;
        p_motor->foc.enc.speed.speedFlt[1].one_minus_a  = (float32_t)MOTOR2_ENC_SPEED_LOCAL_LPF_ONE_M_ALPHA;
        //--- MOTOR COMMAND STRUCTURE -------------------------------------------
        p_motor->foc.cmd.iSat                           = MOTOR2_CURRENT_CMD_SAT_MAX;
        //-----------------------------------------------------------------------
        p_motor->foc.iParkFlt.a                         = MOTOR2_CURRENT_LPF_ALPHA;
        p_motor->foc.iParkFlt.one_minus_a               = MOTOR2_CURRENT_LPF_ONE_M_ALPHA;
        //--- FOC - Initialize duty cycle saturation ----------------------------
        p_motor->foc.dtcMax                             = MOTOR2_DTC_MAX;
        p_motor->foc.dtcMin                             = MOTOR2_DTC_MIN;
        //--- FOC - Encoder test ------------------------------------------------
        p_motor->foc.initPosCnt                         = MOTOR2_POSITION_INIT_EVT;
        p_motor->foc.initFixCnt                         = MOTOR2_FIX_INIT_EVT;
        p_motor->foc.initErr[MIN]                       = MOTOR2_POSITION_INIT_ERR_MIN;
        p_motor->foc.initErr[MAX]                       = MOTOR2_POSITION_INIT_ERR_MAX;
        //--- FOC - Initialize PI controller (Id) -------------------------------
        p_motor->foc.piId.kp                            = (float32_t)MOTOR2_PI_ID_KP_COEF;
        p_motor->foc.piId.ki                            = (float32_t)MOTOR2_PI_ID_KI_COEF;
        //--- FOC - Initialize PI controller (Iq) -------------------------------
        p_motor->foc.piIq.kp                            = (float32_t)MOTOR2_PI_IQ_KP_COEF;
        p_motor->foc.piIq.ki                            = (float32_t)MOTOR2_PI_IQ_KI_COEF;
        //--- DRV IO Config -----------------------------------------------------
        p_motor->drvFaultNum                            = MOTOR2_DRV_FAULT_NUM;
        p_motor->drvEnNum                               = MOTOR2_DRV_EN_NUM;
        //---- PWM config address -----------------------------------------------
        p_motor->epwmBase[CHANNEL_1]                    = MOTOR2_PWM1_BASE;
        p_motor->epwmBase[CHANNEL_2]                    = MOTOR2_PWM2_BASE;
        p_motor->epwmBase[CHANNEL_3]                    = MOTOR2_PWM3_BASE;
    }
    //--- MOTOR ACQUISITION STRUCTURE -------------------------------------------
    p_motor->foc.acq.vBusResultBase                     = VBUS_ADC_RESULT_ADDR;
    p_motor->foc.acq.ppbNum.vBus                        = VBUS_PPB_NUM;
    p_motor->foc.acq.socNum.vBus                        = VBUS_SOC_NUM;
    p_motor->foc.acq.vBusFlt.a                          = VBUS_LPF_ALPHA;
    p_motor->foc.acq.vBusFlt.one_minus_a                = VBUS_LPF_ONE_M_ALPHA;
    p_motor->foc.acq.vExtFlt.a                          = VEXT_LPF_ALPHA;
    p_motor->foc.acq.vExtFlt.one_minus_a                = VEXT_LPF_ONE_M_ALPHA;
    //--- MOTOR ENCORDER STRUCTURE ----------------------------------------------
    p_motor->foc.enc.thetaMech[NEW]                     = 0.0f;
    p_motor->foc.enc.thetaMech[OLD]                     = 0.0f;
    p_motor->foc.enc.thetaIndexRelative                 = 0.0f;
    p_motor->foc.enc.thetaIndexAbsolute                 = 0.0f;
    p_motor->foc.enc.turnNb                             = 0;
    p_motor->foc.enc.flags.all                          = 0U;
    p_motor->foc.enc.speed.speedMech[0]                 = 0.0f;
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

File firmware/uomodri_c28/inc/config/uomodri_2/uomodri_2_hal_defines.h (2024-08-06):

/*
 * File name: omodri_user_defines.h
 * Description: Header file containing user definitions
 */

#ifndef __UOMODRI_2_HAL_DEFINES_H__
#define __UOMODRI_2_HAL_DEFINES_H__

/***********************************************************************
 * INCLUDES
 ***********************************************************************/
#include "device.h"                 // F2838x Headerfile include File

/***********************************************************************
 * GPIO DEFINES
 ***********************************************************************/
#define MOTOR1_PWM1_CHA_NUM                     (0U)
#define MOTOR1_PWM1_CHA_CFG                     GPIO_0_EPWM1A
#define MOTOR1_PWM1_CHA_DEF                     { \
                                                    .pinNum         = MOTOR1_PWM1_CHA_NUM, \
                                                    .fctMux         = MOTOR1_PWM1_CHA_CFG, \
                                                    .direction      = GPIO_DIR_MODE_OUT, \
                                                    .samplingInMode = GPIO_QUAL_ASYNC, \
                                                    .setValue       = false, \
                                                    .intEnable      = false, \
                                                }

#define MOTOR1_PWM1_CHB_NUM                     (1U)
#define MOTOR1_PWM1_CHB_CFG                     GPIO_1_EPWM1B
#define MOTOR1_PWM1_CHB_DEF                     { \
                                                    .pinNum         = MOTOR1_PWM1_CHB_NUM, \
                                                    .fctMux         = MOTOR1_PWM1_CHB_CFG, \
                                                    .direction      = GPIO_DIR_MODE_OUT, \
                                                    .samplingInMode = GPIO_QUAL_ASYNC, \
                                                    .setValue       = true, \
                                                    .intEnable      = false, \
                                                }

#define MOTOR1_PWM2_CHA_NUM                     (2U)
#define MOTOR1_PWM2_CHA_CFG                     GPIO_2_EPWM2A
#define MOTOR1_PWM2_CHA_DEF                     { \
                                                    .pinNum         = MOTOR1_PWM2_CHA_NUM, \
                                                    .fctMux         = MOTOR1_PWM2_CHA_CFG, \
                                                    .direction      = GPIO_DIR_MODE_OUT, \
                                                    .samplingInMode = GPIO_QUAL_ASYNC, \
                                                    .setValue       = false, \
                                                    .intEnable      = false, \
                                                }

#define MOTOR1_PWM2_CHB_NUM                     (3U)
#define MOTOR1_PWM2_CHB_CFG                     GPIO_3_EPWM2B
#define MOTOR1_PWM2_CHB_DEF                     { \
                                                    .pinNum         = MOTOR1_PWM2_CHB_NUM, \
                                                    .fctMux         = MOTOR1_PWM2_CHB_CFG, \
                                                    .direction      = GPIO_DIR_MODE_OUT, \
                                                    .samplingInMode = GPIO_QUAL_ASYNC, \
                                                    .setValue       = true, \
                                                    .intEnable      = false, \
                                                }

#define MOTOR1_PWM3_CHA_NUM                     (4U)
#define MOTOR1_PWM3_CHA_CFG                     GPIO_4_EPWM3A
#define MOTOR1_PWM3_CHA_DEF                     { \
                                                    .pinNum         = MOTOR1_PWM3_CHA_NUM, \
                                                    .fctMux         = MOTOR1_PWM3_CHA_CFG, \
                                                    .direction      = GPIO_DIR_MODE_OUT, \
                                                    .samplingInMode = GPIO_QUAL_ASYNC, \
                                                    .setValue       = false, \
                                                    .intEnable      = false, \
                                                }
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

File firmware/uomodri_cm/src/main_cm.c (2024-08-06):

//
// Included Files
//
//#include <stdint.h>
//#include <stdlib.h>
//#include <stdbool.h>
//#include <string.h>
//#include <float.h>

/***********************************************************************
 * INCLUDES
 ***********************************************************************/
#include <string.h>
#include "main_cm.h"
//#include "foc.h"
#include "communication.h"
#include "uomodri_cm_user_defines.h"
#include "uomodri_cm_hal_config_handlers.h"

/***********************************************************************
 * DEFINES
 ***********************************************************************/

/************************************************************************
 * FUNCTIONS DECLARATION
 ************************************************************************/
inline void IPC_CpuToCmAddrSync(dbg_uart_addr_t*);

/************************************************************************
 * LOCAL VARIABLES
 ************************************************************************/
#pragma DATA_ALIGN(ucControlTable, 1024)
UDMA_ControlTable ucControlTable[32];
dbg_uart_msg_t dbg_uart_tx_msg =
{
 .header[0]         = 'a',
 .header[1]         = 'b',
// .header[2]         = 'c',
// .count             = 0U,
 .ia                = 0.0f,
 .ib                = 0.0f,
 .ic                = 0.0f,
// .vbus              = 0.0f,
// .ialpha            = 0.0f,
// .ibeta             = 0.0f,
 .id                = 0.0f,
 .iq                = 0.0f,
 .iqref             = 0.0f,
 .ud                = 0.0f,
 .uq                = 0.0f,
// .ualpha            = 0.0f,
// .ubeta             = 0.0f,
// .ua                = 0.0f,
// .ub                = 0.0f,
// .uc                = 0.0f,
 .pos               = 0.0f,
// .posref            = 0.0f,
 .vel               = 0.0f,
// .velref            = 0.0f,
// .itcnt             = 0U,
 .crc               = 0,
// .padding           = 0,
};

dbg_uart_addr_t dbg_uart_addr =
{
 .p_ia              = NULL,
 .p_ib              = NULL,
 .p_ic              = NULL,
 .p_vbus            = NULL,
 .p_ialpha          = NULL,
 .p_ibeta           = NULL,
 .p_id              = NULL,
 .p_iq              = NULL,
 .p_ud              = NULL,
 .p_uq              = NULL,
 .p_ualpha          = NULL,
 .p_ubeta           = NULL,
 .p_ua              = NULL,
 .p_ub              = NULL,
 .p_uc              = NULL,
 .p_pos             = NULL,
 .p_posref          = NULL,
 .p_vel             = NULL,
 .p_velref          = NULL,
 .p_iqref           = NULL,
// .p_itcnt           = NULL,
};

/************************************************************************
 * GLOBAL VARIABLES
 ************************************************************************/
extern const hal_cm_t hal_cm;

/***********************************************************************
 * FUNCTIONS DEFINITIONS
 ***********************************************************************/
/**
 * @brief   Main function running on CM processor. MCU init.
 */
void main(void)
{
    uint32_t i = 0;
    // Initialize device clock and peripherals
    CM_init();
    // Hardware Abstraction Layer initialization
    HAL_CM_init(&hal_cm);
    // IPC address translation
    IPC_CpuToCmAddrSync(&dbg_uart_addr);
//    uint32_t command, data;
//    // Get address of ia of MOTOR_1
//    while(!IPC_readCommand(IPC_CM_L_CPU1_R, IPC_CPU1_TO_CM_FLAG, IPC_ADDR_CORRECTION_ENABLE, &command, (uint32_t *)&dbg_uart_addr.p_ia, &data));
//    IPC_ackFlagRtoL(IPC_CM_L_CPU1_R, IPC_CPU1_TO_CM_FLAG);
//    // Get address of ib of MOTOR_1
//    while(!IPC_readCommand(IPC_CM_L_CPU1_R, IPC_CPU1_TO_CM_FLAG, IPC_ADDR_CORRECTION_ENABLE, &command, (uint32_t *)&dbg_uart_addr.p_ib, &data));
//    IPC_ackFlagRtoL(IPC_CM_L_CPU1_R, IPC_CPU1_TO_CM_FLAG);
//    // Get address of ic of MOTOR_2
//    while(!IPC_readCommand(IPC_CM_L_CPU1_R, IPC_CPU1_TO_CM_FLAG, IPC_ADDR_CORRECTION_ENABLE, &command, (uint32_t *)&dbg_uart_addr.p_ic, &data));
//    IPC_ackFlagRtoL(IPC_CM_L_CPU1_R, IPC_CPU1_TO_CM_FLAG);
//    // Get address of vbus of MOTOR_1
//    while(!IPC_readCommand(IPC_CM_L_CPU1_R, IPC_CPU1_TO_CM_FLAG, IPC_ADDR_CORRECTION_ENABLE, &command, (uint32_t *)&dbg_uart_addr.p_vbus, &data));
//    IPC_ackFlagRtoL(IPC_CM_L_CPU1_R, IPC_CPU1_TO_CM_FLAG);
//    // Get address of ialpha of MOTOR_1
//    while(!IPC_readCommand(IPC_CM_L_CPU1_R, IPC_CPU1_TO_CM_FLAG, IPC_ADDR_CORRECTION_ENABLE, &command, (uint32_t *)&dbg_uart_addr.p_ialpha, &data));
//    IPC_ackFlagRtoL(IPC_CM_L_CPU1_R, IPC_CPU1_TO_CM_FLAG);
//    // Get address of ibeta of MOTOR_1
//    while(!IPC_readCommand(IPC_CM_L_CPU1_R, IPC_CPU1_TO_CM_FLAG, IPC_ADDR_CORRECTION_ENABLE, &command, (uint32_t *)&dbg_uart_addr.p_ibeta, &data));
//    IPC_ackFlagRtoL(IPC_CM_L_CPU1_R, IPC_CPU1_TO_CM_FLAG);
//    // Get address of id of MOTOR_1
//    while(!IPC_readCommand(IPC_CM_L_CPU1_R, IPC_CPU1_TO_CM_FLAG, IPC_ADDR_CORRECTION_ENABLE, &command, (uint32_t *)&dbg_uart_addr.p_id, &data));
//    IPC_ackFlagRtoL(IPC_CM_L_CPU1_R, IPC_CPU1_TO_CM_FLAG);
//    // Get address of iq of MOTOR_1
//    while(!IPC_readCommand(IPC_CM_L_CPU1_R, IPC_CPU1_TO_CM_FLAG, IPC_ADDR_CORRECTION_ENABLE, &command, (uint32_t *)&dbg_uart_addr.p_iq, &data));
//    IPC_ackFlagRtoL(IPC_CM_L_CPU1_R, IPC_CPU1_TO_CM_FLAG);
//    // Get address of ud of MOTOR_1
//    while(!IPC_readCommand(IPC_CM_L_CPU1_R, IPC_CPU1_TO_CM_FLAG, IPC_ADDR_CORRECTION_ENABLE, &command, (uint32_t *)&dbg_uart_addr.p_ud, &data));
//    IPC_ackFlagRtoL(IPC_CM_L_CPU1_R, IPC_CPU1_TO_CM_FLAG);
//    // Get address of uq of MOTOR_1
//    while(!IPC_readCommand(IPC_CM_L_CPU1_R, IPC_CPU1_TO_CM_FLAG, IPC_ADDR_CORRECTION_ENABLE, &command, (uint32_t *)&dbg_uart_addr.p_uq, &data));
//    IPC_ackFlagRtoL(IPC_CM_L_CPU1_R, IPC_CPU1_TO_CM_FLAG);
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

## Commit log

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2022-09-08 add all hardware file for the latest udriver3 as a fresh start on master branch
    [ADF6-10-03.5-L-4-2-A-TR.stp, ADM6-10-01.5-L-4-2-A-TR.stp, ASTX-H12.STEP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]
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2022-09-12 Update all files and lib to use new kicad 6 format
    [OMODRI_ANALOG.kicad_sch, OMODRI_Alim_1V2.kicad_sch, OMODRI_Alim_3V3.kicad_sch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]
2022-09-12 Continue routing, split VM an Vpower to improve efficiency with external DC/DC buck converter
    [OMODRI_Alim_5V.kicad_sch, OMODRI_QuadEncod.kicad_sch, OMODRI_driver_M1.kicad_sch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]
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2022-09-13 Change encoder footprint for SMD DF13, continue to route DRVs
    [OMODRI_QuadEncod.kicad_sch, OMODRI_driver_M2.kicad_sch, omodri_laas.kicad_sch]
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2022-09-14 remove the voltage sensing line, not used by the controller and can be recovered from PWM value and model of transistor and dead time
    [OMODRI_driver_M1.kicad_sch, OMODRI_driver_M2.kicad_sch, omodri_laas.kicad_sch]
2022-09-14 Move CAN connector, Include add DC DC back for 1.2 and 3.3V, wire the encoder, ...
    [OMODRI_CAN.kicad_sch, OMODRI_QuadEncod.kicad_sch, omodri_laas.kicad_sch]
2022-09-15 Add 12V DC/DC to unload DRV LDO when working with high voltages
    [OMODRI_Alim_12V.kicad_sch, OMODRI_power.kicad_sch, omodri_laas.kicad_sch]
2022-09-20 Use angle DF13 connector for SPI, CAN and encoders, add 3d step files, route
    [DF13-2P-1.25H.stp, DF13-5P-1.25H.stp, DF13A-2P-1.25H.stp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]
2022-09-21 Almost done, Rework power plane, change FSI DF13 (possibly wrong footprint (see pin 1), add 3d for all components, connect VM and 12V0, ...
    [DF13-7P-1.25H.stp, FC4L32R050FER.stp, OMODRI_FSI_RX.kicad_sch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]
2022-09-23 fix df13 7pin footprint, continue routing
    [omodri_laas.kicad_sch]
2022-09-30 Schematics update. 12V0 and 5V0 power supplies not finished yet. RS485 added but not connected to F28388 mcu.
    [OMODRI_ANALOG.kicad_sch, OMODRI_Alim_12V.kicad_sch, OMODRI_Alim_1V2.kicad_sch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]
2022-10-25 Temporary version of udrive3 v2.0. - In schematic there are 2 solutions for DC/DC buck converter. - PCB routing is not finished yet.
    [DF13-10P-1.25DSA.stp, DF13A-4P-1.25H.stp, DF13A-6P-1.25H.stp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]
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2022-11-09 Power supplies updates. Previous 12V & 5V need to be removed.
    [OMODRI_ANALOG.kicad_sch, OMODRI_Alim_5V.kicad_sch, OMODRI_FSI_TX.kicad_sch]
2022-11-13 ORouting in progress. REF 3V0 missing.
    [OMODRI_Alim_12V.kicad_sch, OMODRI_Alim_5V.kicad_sch, OMODRI_CAN_RS845.kicad_sch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]
2022-11-18 PCB fully routed. Some optimizations need to be done + revue of the schematics.
    [OMODRI_Alim_12V.kicad_sch, OMODRI_Alim_5V.kicad_sch, OMODRI_CAN_RS845.kicad_sch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]
2022-11-20 PCB update. Re-annotation of the design + via stitching (GND).
    [OMODRI_ANALOG.kicad_sch, OMODRI_Alim_12V.kicad_sch, OMODRI_Alim_1V2.kicad_sch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]
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2022-11-22 PCB updates. - Replace CAN/RS485 120ohm resistor - Replace resistor on TCAN RXD pin - Update of some references - Add some 3D missing models
    [ECS-TXO-2016.step, ESD321DPYR.stp, OMODRI_Alim_12V.kicad_sch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]
2022-11-24 PCB updates - FSI protection added against FPC cable reverse connection - BOSCH BMI088 IMU added.
    [OMODRI_ANALOG.kicad_sch, OMODRI_Alim_12V.kicad_sch, OMODRI_Alim_1V2.kicad_sch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]
2022-11-25 PCB udpates. - add serial resistors on boot jumpers - modify config jumpers to be opened by default
    [OMODRI_ANALOG.kicad_sch, OMODRI_Alim_12V.kicad_sch, OMODRI_Alim_1V2.kicad_sch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]
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2022-11-28 Gerber update, missing ordering reference added and project BOM.
    [OMODRI_Alim_5V.kicad_sch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]
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2022-11-30 Solve an issue on a keepout area.
    [omodri_laas-B_Cu.gbl, omodri_laas-B_Mask.gbs, omodri_laas-B_Silkscreen.gbo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]
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2022-12-02 Issue on implantation_bottom.pdf file solved.
    [omodri_laas-B_Cu.gbl, omodri_laas-B_Mask.gbs, omodri_laas-B_Silkscreen.gbo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]
2022-12-08 Issues solved on PCB to be build. - Drills too close to the edge board. - Mechanical pads of power transistor too close to edge board. - Some JTAG tracks didn't respect edge clearance.
    [omodri_laas-B_Cu.gbl, omodri_laas-B_Mask.gbs, omodri_laas-B_Silkscreen.gbo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]
2022-12-22 Final version of uOmodri V2r1 send in production.
    [omodri_laas-B_Cu.gbl, omodri_laas-B_Mask.gbs, omodri_laas-B_Silkscreen.gbo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]
2023-01-23 Fab update. Solder paste (top & bottom) masks updated + placement files.
    [omodri_laas-B_Paste.gbp, omodri_laas-F_Paste.gtp, omodri_laas-job.gbrjob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]
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2023-02-17 2 issues fixed: -UART debug communication is working now. -Sometimes after alignment procedure, motor was running at full speed in opposite direction. Solved forcing a movement of motor at startup.
    [communication.h, communication_cm.c, hal.c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]
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2023-03-01 Issue on index detection solved. Index was previously gated (coupled with strobe source ADCSOCA or ADCSOCB).
    [communication.c, communication.h, main.c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]
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2024-02-07 First release of uOmodri v3. Swap COM SPI. Modify CAN to CAN FD and bus sharing with RS485.
    [OMODRI_ANALOG.kicad_sch, OMODRI_Alim_12V.kicad_sch, OMODRI_Alim_1V2.kicad_sch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]
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2024-02-14 Modify JP5/JP6 jumper to remove DRC error. Add gate resistor on power MOSFET (high & low side).
    [OMODRI_ANALOG.kicad_sch, OMODRI_Alim_12V.kicad_sch, OMODRI_Alim_1V2.kicad_sch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]
2024-02-16 update 3D models. Modify the SPI CS debug pin previously shared with boot function. Regen gerber files.
    [BMI088--3DModel-STEP-56544.STEP, C5750X7S2A226M280KB.STEP, OMODRI_GPIO.kicad_sch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]
2024-02-26 Update of the load connect/disconnect on the CAN/RS485 bus. Remove the electronic switch replaced by a 1.27mm jumper.
    [OMODRI_Alim_12V.kicad_sch, OMODRI_Alim_1V2.kicad_sch, OMODRI_Alim_3V3.kicad_sch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]
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2024-03-01 Update PCB layout to match JLCPCB requirements (via diameter). Set Netclass constraints defined in uOmodri_v2.
    [OMODRI_ANALOG.kicad_sch, OMODRI_Alim_12V.kicad_sch, OMODRI_Alim_1V2.kicad_sch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]
2024-03-07 Add snubbers on motors phases & resistors on high side gates. Update BOM list.
    [OMODRI_Alim_12V.kicad_sch, OMODRI_Alim_1V2.kicad_sch, OMODRI_Alim_3V3.kicad_sch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]
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2024-03-19 Update of uOmodri_V3 replacing TCAN3413 by TCAN330G and adding sync on IMU.
    [OMODRI_CAN_RS845.kicad_sch, OMODRI_GPIO.kicad_sch, OMODRI_IMU_DBG.kicad_sch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]
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2024-03-19 Update BOM list including TCAN refs. Update Gerber + pos + drills files.
    [OMODRI_CAN_RS845.kicad_sch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]
2024-05-03 Update of uOmodri V3. Correct pinning of CAN/RS485 connector.
    [ADF6-10-03.5-L-4-2-A-TR.stp, ADF6-10-07.5-L-4-2-A-TR.stp, ADM6-10-01.5-L-4-2-A-TR.stp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]
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2024-05-15 Update of the multicolor led footprints in uOmodri V3.1 & uOmodri_SA V1.0.
    [OMODRI_LED_dbg.kicad_sch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]
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2024-05-23 Immunity improvement on uOmodri V3. Stack up change from 6 to 8 layers.
    [omodri_laas-B_Cu.gbl, omodri_laas-B_Mask.gbs, omodri_laas-B_Paste.gbp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]
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2024-05-26 Update of uOmodri_SA V1.0. Add a multicolor led + increase the copper to edge clearance + modify the NPTH
    [OMODRI_LED_dbg.kicad_sch, OMODRI_USB.kicad_sch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]
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2024-05-28 Update some reference on uOmodri V3.1 for fab. Update uOmodri_SA V1.0 reducing heights of top layers components.
    [KEYSTONE_5015.step, OMODRI_Alim_1V2.kicad_sch, OMODRI_Alim_3V3.kicad_sch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]
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2024-06-19 Update a led ref on uOmodri V3, update the implentation files for uOmodri_SA.
    [OMODRI_driver_M1.kicad_sch, OMODRI_driver_M2.kicad_sch]
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2024-08-07 Update of the interrupt errata function. Add of CLB files for RTL simulation.
    [communication.c, hal.c, hal.h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]
2024-09-05 Replace the TCAN330G (5Mbps) by TCAN3414 (8Mbps) on both designs.
    [OMODRI_CAN_RS845.kicad_sch, OMODRI_GPIO.kicad_sch, OMODRI_mcu.kicad_sch]
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2024-11-08 Update on uOmodri_SA. Remove USB, com SPI & debug connectors for integration into Myactuator motors. Connectors replaced by a ZIF connector.
    [MOLEX_5034801400.stp, MOLEX_5034802000.stp, MOLEX_5051101492.stp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]
2024-11-12 Update on uOmodri_SA. Move multicolor LED, add +3.3V & &+5V on ZIF connector. Update bottom silkscreen layer (adding names for the ZIF connector).
    [OMODRI_LED_dbg.kicad_sch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]
2024-12-19 Update schematics & layout adding a 100kohm pull down resistor on USB Vbus to detect usb connect/disconnect.
    [OMODRI_ANALOG.kicad_sch, OMODRI_Alim_12V.kicad_sch, OMODRI_Alim_1V2.kicad_sch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]
2025-02-14 New schematics of single axis controller with shunt resistors on motor phases.
    [AMASS_MR30PB-FB.step, AMASS_MR30PW-FB.STEP, AMASS_MR30PW-M.STEP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]
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2025-03-25 Udriver3 Single Axis V2. Update on RS485 communication (add McBSP + CLB).
    [OMODRI_GPIO.kicad_sch, OMODRI_mcu.kicad_sch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]

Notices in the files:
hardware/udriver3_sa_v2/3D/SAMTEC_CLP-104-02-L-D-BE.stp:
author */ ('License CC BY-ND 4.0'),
